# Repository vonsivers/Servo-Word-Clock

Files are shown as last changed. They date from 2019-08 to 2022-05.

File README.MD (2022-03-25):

# Servo Wordclock - Version 2

Wordclock controlled by 114 servos. Improved version 2

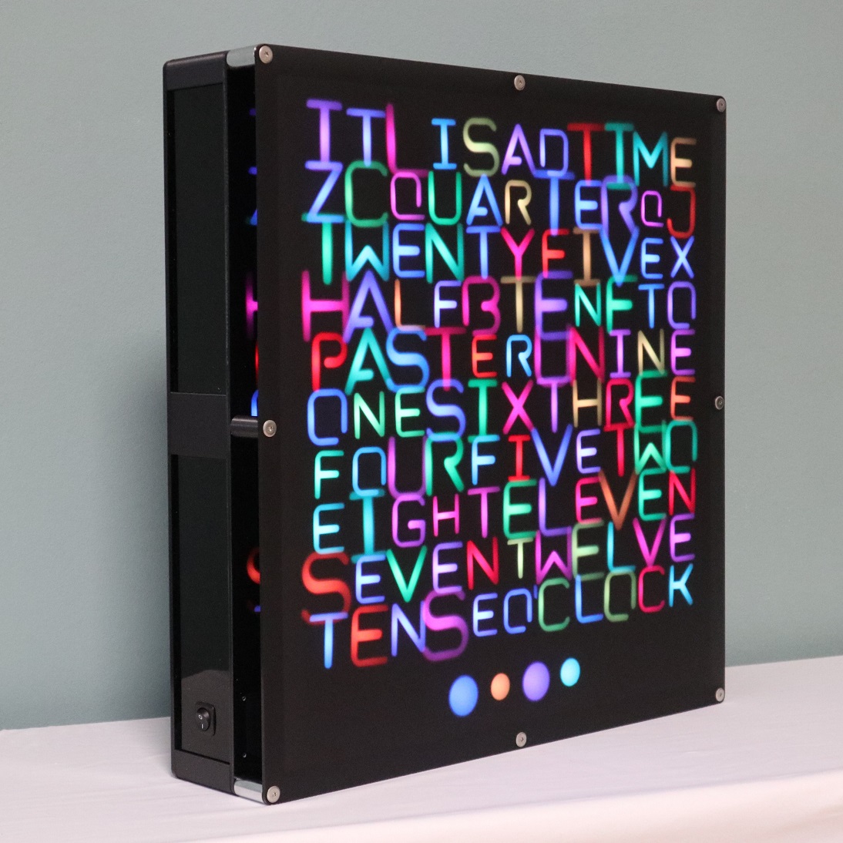
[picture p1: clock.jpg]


## BoM
see "BoM.xls"

## Detailed Build Instructions
see "Assembly Instructions.pdf"

## Laser Cut
see files in folder dxf

quantity, materials and thicknesses specified in BoM

## 3D Printing
see files in folder stl

quantity and recommended materials specified in BoM

stl files named "Any" have slightly looser tolerances

## PCBs
see folder PCBs

LED_board was ordered as PCBA from PCBWay.com with black solder mask

wordclock_mainPCB was ordered as bare PCB from aisler.net

## Links
[demo video on YouTube](https://youtu.be/Euf8V2k0oOI)

[Hackaday.io project link](https://hackaday.io/project/166546-servo-controlled-word-clock-v2)

[Instructables project link](https://www.instructables.com/Servo-Wordclock-V2/)

[Version 1 Instructables project link](https://www.instructables.com/Word-Clock-Controlled-by-114-Servos/)

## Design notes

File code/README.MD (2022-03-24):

# Servo Word Clock GUI - Version 2
> Code for Servo Word Clock for ESP8266

Allows control of clock via webserver that runs on ESP. GUI based on preact material UI. 

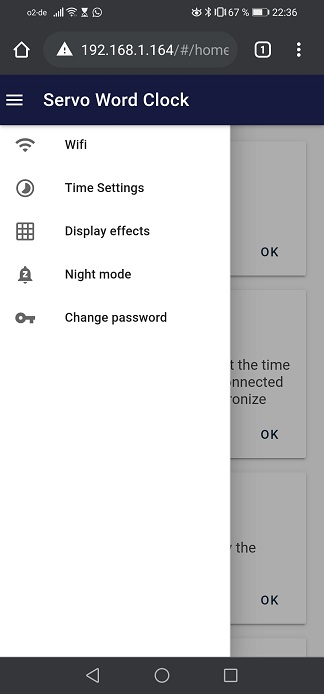
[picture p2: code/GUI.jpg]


## Build

- Install [node js](https://nodejs.org/en/)

- open terminal in folder "servowordclock-gui-develop"

```sh
npm i

npm run build
```

## Code Upload

- Install Arduino IDE

- Install ESP8266 addon

- Install ESP8266LittleFS tool

- Install required libraries
	- https://github.com/me-no-dev/ESPAsyncTCP
	- https://github.com/me-no-dev/ESPAsyncWebServer
	- https://github.com/adafruit/Adafruit-PWM-Servo-Driver-Library
	- https://github.com/FastLED/FastLED

- in Arduino IDE select Tools -> Boards -> ESP8266 Boards -> Node MCU 1.0 (ESP-12E)

- Upload LittleFS Data using Arduino IDE

- Upload code to ESP using Arduino IDE

- Once code has been uploaded following updates can be done via Wifi (OTA) with password "ServoWordClockOTA"

## Code Manual

see Manual.pdf

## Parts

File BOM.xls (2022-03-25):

# | Name | Description | Qty | Type | Material | comment | included in Kit | source | Item No.
1 | Screen V3_4 | 3mm thickness | 1 | Lasercut | Acrylic, grey, frosted, translucent |  | yes | https://expresszuschnitt.de/Acrylglas-satiniert-grau | AGS-9T23XX
2 | Frame V3_4 | 5mm thickness | 1 | Lasercut | Acrylic, black |  | yes | snijlab.nl
3 | Backplate V3_4 | 5mm thickness | 1 | Lasercut | Acrylic, black or clear |  | yes | snijlab.nl
4 | Cover | 3mm thickness | 7 | Lasercut | Acrylic, black or clear |  | yes | snijlab.nl
5 | Cover Switch | 3mm thickness | 1 | Lasercut | Acrylic, black or clear |  | yes | snijlab.nl
6 | Corner Column V3_4 |  | 3 | 3D-Print | PETG/PLA | PETG recommend | no | /
7 | Corner Column Cable V3_4 |  | 1 | 3D-Print | PETG/PLA | PETG recommend | no | /
8 | Top Down Column V3_4 |  | 2 | 3D-Print | PETG/PLA | PETG recommend | no | /
9 | Side Column V3_4 |  | 2 | 3D-Print | PETG/PLA | PETG recommend | no | /
10 | Corner Column Front V3_4 |  | 4 | 3D-Print | PETG/PLA | PETG recommend | no | /
11 | Cable Holder V3_5 |  | 1 | 3D-Print | PETG/PLA |  | no | /
12 | Screw Cover V3_5 |  | 2 | 3D-Print | PETG/PLA |  | no | /
13 | Housing 4x V3_5 |  | 1 | 3D-Print | PETG/PLA | PETG recommend | no | /
14 | Spur Gear M1 Z20 - V3_4 |  | 4 | 3D-Print | PETG/PLA | PETG recommend "may need be adjusted according to printer tolerances, fitting to Housing and Gear" | no | /
15 | Spur Rack V3_5 |  | 114 | 3D-Print | PETG/PLA | PETG recommend "may need be adjusted according to printer tolerances, fitting to Housing and Gear" | no | /
16 | Housing V3_5 Top |  | 11 | 3D-Print | PETG/PLA | PETG recommend | no | /
17 | Housing V3_5 Bottom |  | 11 | 3D-Print | PETG/PLA | PETG recommend | no | /
18 | Standoff M2,5 x 2,5 |  | 44 | 3D-Print | PETG/PLA |  | no | /
19 | Standoff M3 x 5 |  | 4 | 3D-Print | PETG/PLA |  | no | /
20 | Standoff M2,5 x 5,5 |  | 3 | 3D-Print | PETG/PLA |  | no | /
21 | A V3_2 |  | 4 | 3D-Print | PETG/PLA |  | no | /
22 | B V3_2 |  | 1 | 3D-Print | PETG/PLA |  | no | /
23 | C V3_2 |  | 3 | 3D-Print | PETG/PLA |  | no | /
24 | D V3_2 |  | 1 | 3D-Print | PETG/PLA |  | no | /
25 | E V3_2 |  | 21 | 3D-Print | PETG/PLA |  | no | /
26 | F V3_2 |  | 5 | 3D-Print | PETG/PLA |  | no | /
27 | G V3_2 |  | 1 | 3D-Print | PETG/PLA |  | no | /
28 | H V3_2 |  | 3 | 3D-Print | PETG/PLA |  | no | /
29 | I V3_2 |  | 8 | 3D-Print | PETG/PLA |  | no | /
30 | J V3_2 |  | 1 | 3D-Print | PETG/PLA |  | no | /
31 | K V3_2 |  | 1 | 3D-Print | PETG/PLA |  | no | /
32 | L V3_2 |  | 5 | 3D-Print | PETG/PLA |  | no | /
33 | M V3_2 |  | 1 | 3D-Print | PETG/PLA |  | no | /
34 | N V3_2 |  | 8 | 3D-Print | PETG/PLA |  | no | /
35 | O V3_2 |  | 5 | 3D-Print | PETG/PLA |  | no | /
36 | O' V3_2 |  | 1 | 3D-Print | PETG/PLA |  | no | /
37 | P V3_2 |  | 1 | 3D-Print | PETG/PLA |  | no | /
38 | Point V3_2 |  | 4 | 3D-Print | PETG/PLA |  | no | /
39 | Q V3_2 |  | 2 | 3D-Print | PETG/PLA |  | no | /
40 | R V3_2 |  | 5 | 3D-Print | PETG/PLA |  | no | /
41 | S V3_2 |  | 5 | 3D-Print | PETG/PLA |  | no | /
42 | T V3_2 |  | 13 | 3D-Print | PETG/PLA |  | no | /
43 | U V3_2 |  | 3 | 3D-Print | PETG/PLA |  | no | /
44 | V V3_2 |  | 5 | 3D-Print | PETG/PLA |  | no | /
45 | W V3_2 |  | 3 | 3D-Print | PETG/PLA |  | no | /
46 | X V3_2 |  | 2 | 3D-Print | PETG/PLA |  | no | /
47 | Y V3_2 |  | 1 | 3D-Print | PETG/PLA |  | no | /
48 | Z V3_2 |  | 1 | 3D-Print | PETG/PLA |  | no | /
49 | Diffusor Film - Aslan D160 | Folie Aslan D160 49x48 cm | 1 | Foil | PVC |  | yes | https://www.ifoha.de/shop/spezialfolien/folien-fuer-werbetechnik/leuchtkastenfolie/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 | 14160
50 | Wordclock LED PCB | PCBA | 114 | PCBA | div. | Servo-Word-Clock\PCBs\LED_board | yes | PCBway.com
51 | Wordclock Main PCB | bare PCB | 1 | PCB | div. | Servo-Word-Clock\PCBs\wordclock_mainPCB | yes | aisler.net
52 | ESP8266 Dev Board | NodeMCU Lua Amica Modul V2 ESP8266 ESP-12F WIFI | 1 | PCBA | div. |  | yes | https://www.az-delivery.de/products/nodemcu?variant=27600517385
53 | TXS0108E v1 | 8 ch logic level converter | 1 | PCBA | div. |  | yes | https://www.az-delivery.de/products/logiklevel-wandler-3-3v-5v?variant=18568538390624
54 | Resistor, 470 Ohm | Through Hole | 1 | Electronics | div. |  | yes | https://www.conrad.de/de/p/tru-components-tc-cfr0w4j0471a50203-kohleschicht-widerstand-470-axial-bedrahtet-0207-0-25-w-5-1-st-1584807.html
55 | Electrolytic Capacitor, 6.3V, 1000µF | Through Hole | 1 | Electronics | div. |  | yes | https://www.conrad.de/de/p/teapo-ksh108m016s1a5g20k-elektrolyt-kondensator-radial-bedrahtet-3-5-mm-1-000-f-16-v-20-x-h-8-mm-x-20-mm-1-st-1590551.html
56 | JST XH2.54 connector, male, 2-pin | Through Hole | 1 | Electronics | div. |  | yes | https://www.ebay.de/itm/173782755881?hash=item2876426a29:g:E0QAAOSwliBgG6Ys
57 | JST XH2.54 connector, male, 3-pin | Through Hole | 1 | Electronics | div. |  | yes | https://www.ebay.de/itm/173782755881?hash=item2876426a29:g:E0QAAOSwliBgG6Ys
58 | male pin header, 2.54mm, 3-pin |  | 1 | Electronics | div. |  | yes | https://www.ebay.de/itm/255283310862
59 | Current Distributor V2x12 |  | 2 | PCBA | div. |  | yes | https://www.pollin.de/ | 452459
60 | PCA9685 PWM driver | 12 Channel PWM driver | 11 | PCBA | div. |  | yes | https://www.az-delivery.de/products/pca9685-servotreiber?variant=6126640889883
61 | Male Pin Header 6-Pin | angled/horizontal | 11 | Electronics | div. |  | yes | https://www.mouser.de/ | 649-68016-406HLF
62 | Servo - SG90 |  | 114 | Servodrive | div. | 6 spare pcs included in kit | yes | https://de.aliexpress.com
63 | Rocker Switch - Conrad - 1587816 | TRU COMPONENTS Wippschalter TC-R13-135A-02 250 V/AC 10 A 1 x Aus/Ein rastend 1 St. | 1 | Electronics | div. |  | yes | https://www.conrad.de/de/p/tru-components-wippschalter-tc-r13-135a-02-250-v-ac-10-a-1-x-aus-ein-rastend-1-st-1587816.html
64 | Zip Tie Mount |  | 93 | OTS | PA6 |  | yes | https://www.ebay.de/
65 | Rampa - KF M6x16 |  | 12 | Screw | Steel, black |  | yes | https://www.rampa.com/de/de/
66 | Rampa - KF M6x90 |  | 4 | Screw | Steel, black |  | yes | https://www.rampa.com/de/de/
67 | ISO 7380 - M3 x 12 |  | 4 | Screw | Steel, black |  | yes | schraube-mutter.de
68 | ISO 7380 - M4 x 8 |  | 1 | Screw | Steel, black |  | yes | schraube-mutter.de
69 | ISO 10642 - M4 x 12 |  | 24 | Screw | Steel, black |  | yes | schraube-mutter.de
70 | ISO 7045 - M2,5 x 4 | included with servo | 114 | Screw | Steel |  | yes | /
71 | ISO 7049 - ST2,2 x 6 |  | 376 | Screw | Steel |  | yes | https://www.schraubenhimmel.de/detail/index/sArticle/47778
72 | ISO 7049 - ST2,2 x 6,5 | included with servo | 228 | Screw | Steel |  | yes | /
73 | ISO 4762 - M2,5 x 12 |  | 3 | Screw | Steel, black |  | yes | schraube-mutter.de
74 | Zip Ties |  | 100 | OTS | PA6 |  | yes | https://www.ebay.de/
75 | Cable sleeve 0.34mm² |  | 18 | Electronics | div. |  | yes | https://www.conrad.de/de/p/tru-components-1091301-aderendhuelse-1-x-0-34-mm-x-6-mm-teilisoliert-tuerkis-100-st-1567720.html | 1567720 - VQ
76 | Cable sleeve 0.22mm² |  | 22 | Electronics | div. |  | yes | https://www.conrad.de/de/p/tru-components-1091302-aderendhuelse-1-x-0-25-mm-x-6-mm-teilisoliert-violett-100-st-1571001.html | 1571001 - VQ
77 | power supply, 5V, 5A | Mean Well GST40A05-P1J power supply, 5 V/DC, 5 A, 25 W | 1 | Electronics | div. |  | yes | https://www.conrad.de/de/p/mean-well-gst40a05-p1j-tischnetzteil-festspannung-5-v-dc-5-a-25-w-1439222.html | 1439222 - VQ
78 | Mainpower Cable 230/110V |  | 1 | Cable | div. | depends on region | yes | https://www.conrad.de
79 | Cable Mainpower 5V with plug | DC cable, 5.50 mm, 2.10 mm, plug - open end, 1 m | 1 | Cable | div. |  | yes | https://www.conrad.de/de/p/tru-components-niedervolt-anschlusskabel-niedervolt-buchse-kabel-offenes-ende-5-50-mm-2-10-mm-1-m-1-st-1715115.html | 1715115 - VQ
80 | Cable 5V-Block | Cable, red, 0.34mm², open end - sleeve, 7.5 cm | 1 | Cable | div. | DIY | yes | /
81 | Cable 5V Block-Block | Cable, red, 0.34mm², sleeve - sleeve, 12 cm | 1 | Cable | div. | DIY | yes | /
82 | Cable Gnd Block-Block | Cable, black, 0.34mm², sleeve - sleeve, 12 cm | 1 | Cable | div. | DIY | yes | /
83 | Cabel LED-LED short | Cable JST XH2.54, 3-pole, female-female, 7.5 cm, 22AWG | 103 | Cable | div. |  | yes | https://de.aliexpress.com/store/5031112?spm=a2g0s.9042311.0.0.77f84c4dC5KDAi
84 | Cable LED-LED long | Cable JST XH2.54, 3-pole, female-female, 55 cm, 22AWG | 12 | Cable | div. |  | yes | https://de.aliexpress.com/store/5031112?spm=a2g0s.9042311.0.0.77f84c4dC5KDAi
85 | Cable 1st Sboard | Cable Dupont, 3-pole, female-female, 25 cm | 1 | Cable | div. |  | yes | https://de.aliexpress.com/item/33030664287.html?spm=a2g0s.9042311.0.0.70284c4ds6bReA
86 | Cable Sboard-Sboard | Cable Dupont, 6-pole, female-female, 10 cm | 10 | Cable | div. |  | yes | https://de.aliexpress.com/item/33030664287.html?spm=a2g0s.9042311.0.0.70284c4ds6bReA
87 | Cable Sboard-5V | Cable, red, 0.22mm², sleeve - sleeve, ca. 25 cm | 11 | Cable | div. | DIY, varying length | yes | /
88 | Cable Sboard-Gnd | Cable, black, 0.22mm², sleeve - sleeve, ca. 25 cm | 11 | Cable | div. | DIY, varying length | yes | /
89 | Cable Main PCB Power | Cable JST XH2.54, 2-pole, female-sleeve, 10 cm, 22AWG | 1 | Cable | div. |  | yes | /
90 | Glueing Tool |  | 1 | 3D-Print | PETG/PLA |  | no | /
91 | Alignment Jig |  | 1 | 3D-Print | PETG/PLA |  | no | /

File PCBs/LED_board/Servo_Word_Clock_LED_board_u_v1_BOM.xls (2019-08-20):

 |  |  | Servo Word Clock LED board u v1 BOM
Item # | *Ref Des | *Qty | Manufacturer | *Mfg Part # | Description / Value | *Package | Type | Your Instructions / Notes
1 | U1 | 1 | Worldsemi Co Limited | WS2812B | LED, SMD, 5050,PLCC4, RGB | PLCC4 | SMD
2 | C1 | 1 | Murata | GCJ188R71C104KA01D | CAP CER 0.1UF 16V 10% X7R 0603 | 0603 | SMD
3 | J1,J2 | 2 | JST | B3B-XH-A(LF)(SN) | CONN HEADER VERT 3POS 2.5MM | 3POS | thru-hole | Assembled on bottom side!
Need a quick and accurante quote? Need an efficient production? Please read?MT Ordering Necessary Files & Info?n 1 minute. Thank you very much!
Click for Instructions on How to Create a BOM

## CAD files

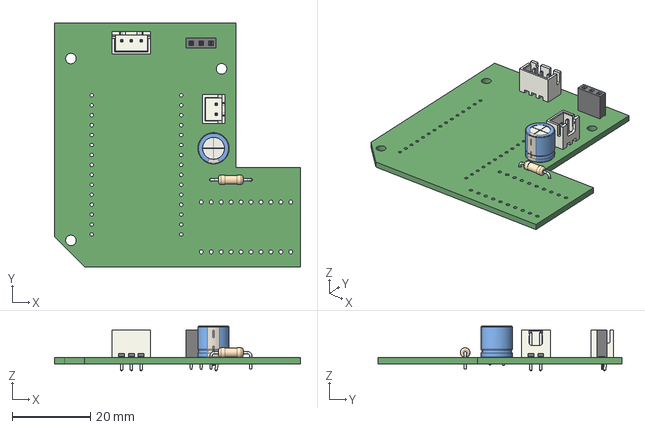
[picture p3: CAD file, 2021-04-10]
PCBs/wordclock_mainPCB/wordclock_mainPCB.step
62.9 x 62.2 x 11.4 mm

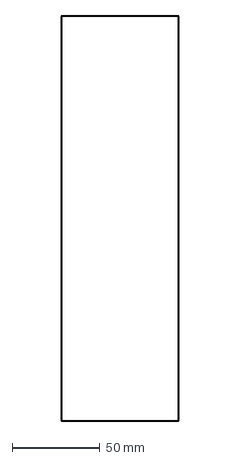
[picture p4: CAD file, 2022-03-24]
dxf/Cover.dxf
67.0 x 231.0 mm

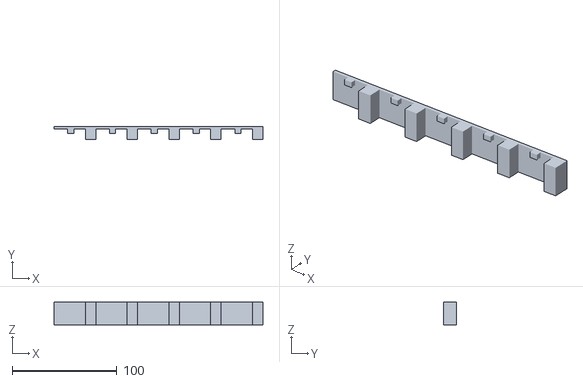
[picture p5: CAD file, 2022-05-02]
stl/alignment jig.stl
200.0 x 12.5 x 22.0

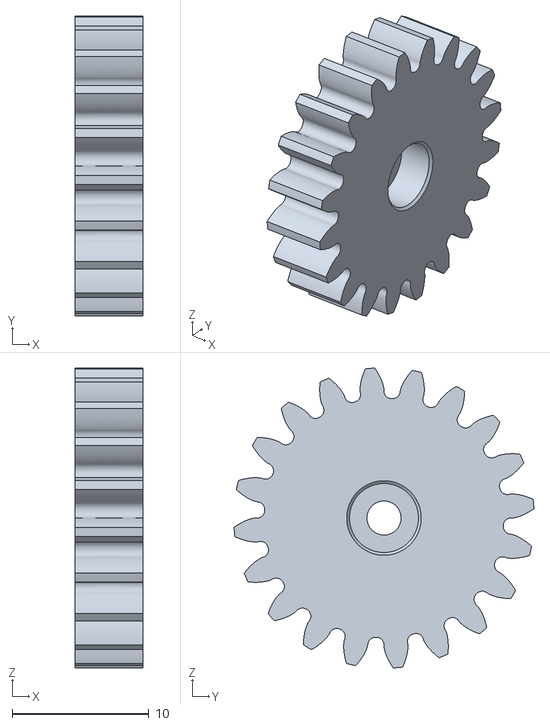
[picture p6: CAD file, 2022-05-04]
stl/Letter/Spur Gear M1 Z20 - D5,05.stl
5.00 x 22.0 x 22.0

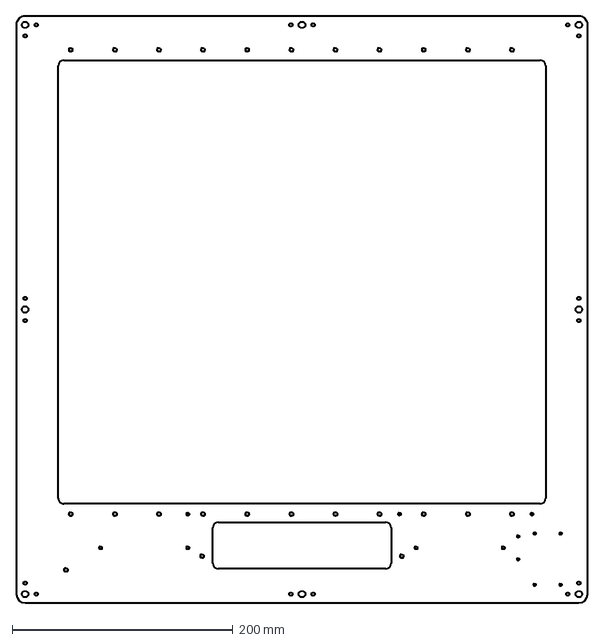
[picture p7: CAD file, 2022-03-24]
dxf/Frame V3_4.dxf
518.0 x 532.0 mm

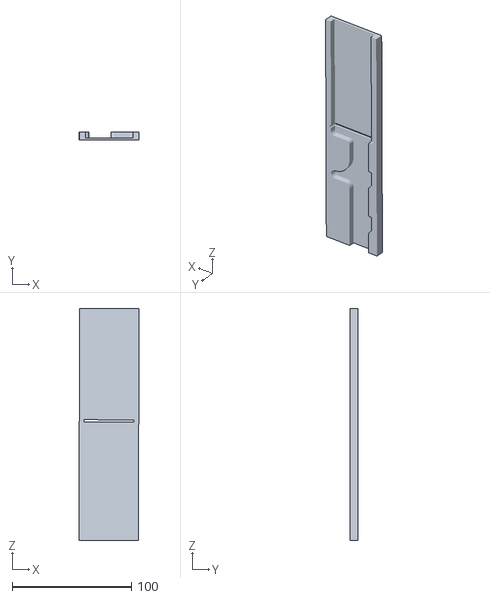
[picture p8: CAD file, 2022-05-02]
stl/glueing jig.stl
50.5 x 7.06 x 194.3

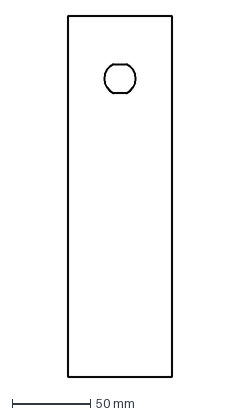
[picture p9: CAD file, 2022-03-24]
dxf/Cover Switch.dxf
67.0 x 231.0 mm

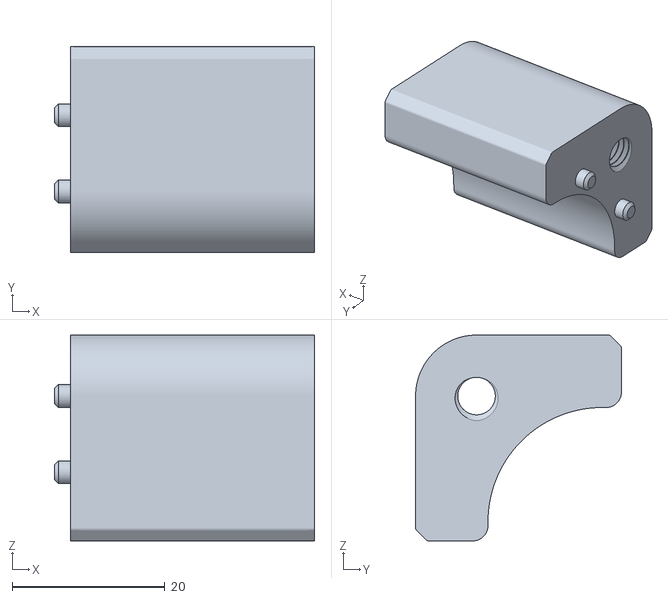
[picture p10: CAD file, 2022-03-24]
stl/Corner Column Front V3_4.stl
34.1 x 27.0 x 27.0

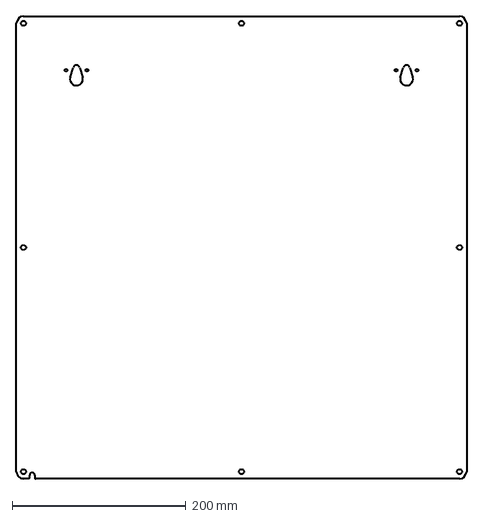
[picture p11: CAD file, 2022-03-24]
dxf/Backplate V3_4.dxf
518.0 x 532.0 mm

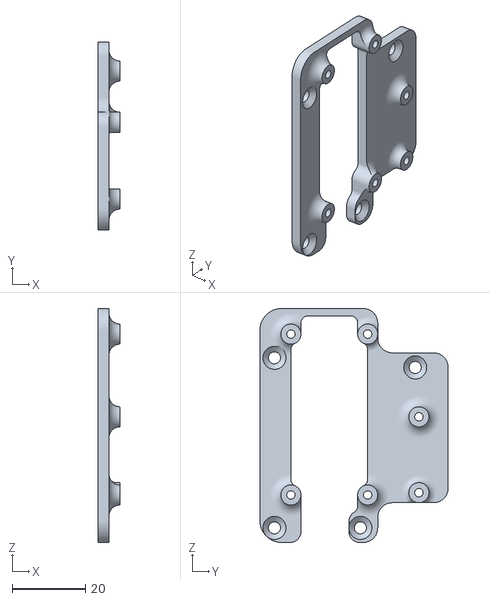
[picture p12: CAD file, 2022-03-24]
stl/ESP Holder V2.stl
6.00 x 51.5 x 64.0

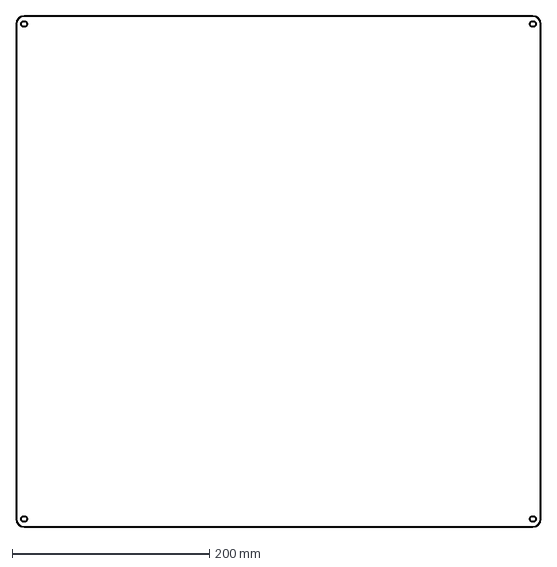
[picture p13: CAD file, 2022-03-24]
dxf/Screen V3_4.dxf
532.0 x 518.0 mm

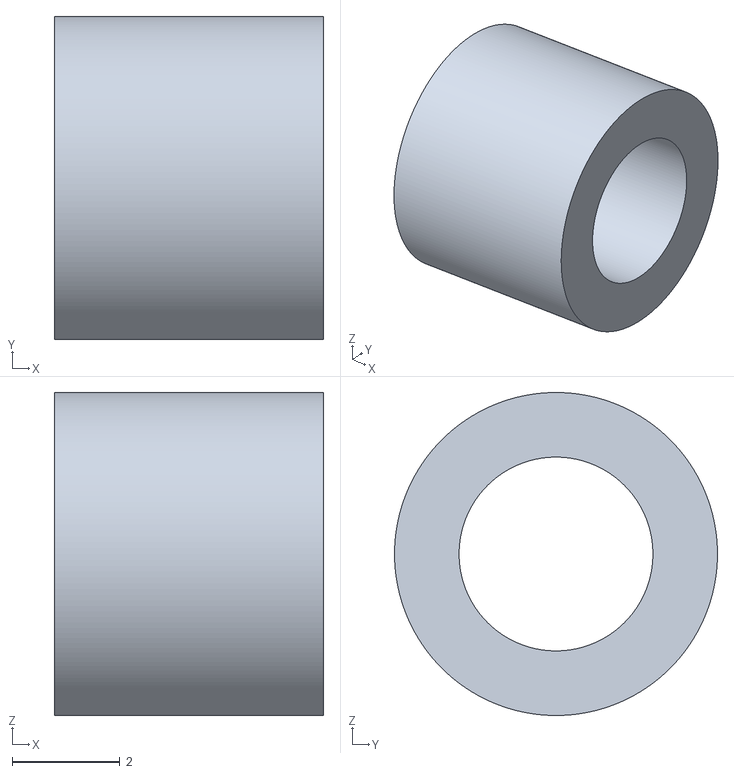
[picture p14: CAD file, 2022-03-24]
stl/Standoff M3 x 5.stl
5.00 x 6.00 x 6.00

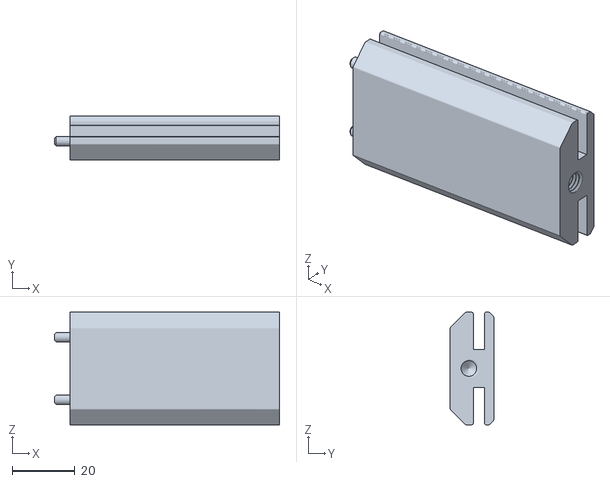
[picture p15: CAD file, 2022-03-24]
stl/Top Down Column V3_4 Any.stl
71.9 x 14.0 x 36.0

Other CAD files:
stl/Letter/Spur Gear M1 Z20 - D5,1.stl
stl/Letter/Spur Gear M1 Z20 - D5.stl
stl/Letter/Spur Gear M1 Z20 - D4,85.stl
stl/Letter/Spur Gear M1 Z20 - D4,95.stl
stl/Letter/Spur Gear M1 Z20 - D4,9.stl
stl/Cable Holder V3_5.stl
stl/Corner Column Cable V3_4 Any.stl
stl/Corner Column Cable V3_4.stl
stl/Corner Column V3_4 Any.stl
stl/Corner Column V3_4.stl
stl/Letter/A V3_15.stl
stl/Letter/B V3_15.stl
stl/Letter/C V3_15.stl
stl/Letter/D V3_15.stl
stl/Letter/E V3_15.stl
stl/Letter/F V3_15.stl
stl/Letter/G V3_15.stl
stl/Letter/H V3_15.stl
stl/Letter/I V3_15.stl
stl/Letter/J V3_15.stl
stl/Letter/K V3_15.stl
stl/Letter/L V3_15.stl
stl/Letter/M V3_15.stl
stl/Letter/N V3_15.stl
stl/Letter/O V3_15.stl
stl/Letter/O' V3_15.stl
stl/Letter/P V3_15.stl
stl/Letter/Point V3_15.stl
stl/Letter/Q V3_15.stl
stl/Letter/R V3_15.stl
stl/Letter/S V3_15.stl
stl/Letter/T V3_15.stl
stl/Letter/U V3_15.stl
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

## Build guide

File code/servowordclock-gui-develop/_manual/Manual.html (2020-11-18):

 User Manual



User Manual

Introduction

Setting up the Clock

Access User Interface

Timezone Configuration

Manual Time Setting

Display Settings

Night Mode Settings

## Introduction

The Servo Wordclock was designed to be connected to your local WiFi and can be controlled via a web based user interface. With internet access the clock will also automatically keep time by synchronizing to an NTP server.

If there is no WiFi network available the clock will create a WiFi access point to which other devices can connect.

The user interface can be used to control all clock functions like WiFi configuration, time setting, display brightness, color and animations.

All settings will be permanently stored on the clock’s non-volatile memory.

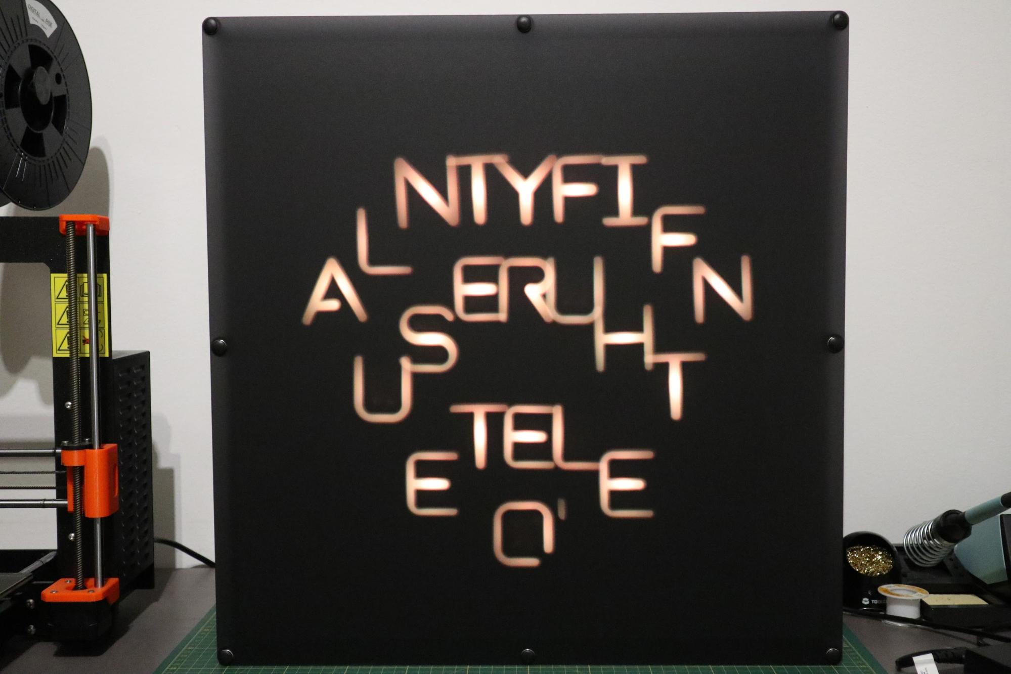
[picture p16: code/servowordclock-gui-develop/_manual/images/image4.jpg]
## Setting up the Clock 

- Connect the clock to the included power supply
- To turn on the clock use the switch located on the lower left side. The clock will need about 30 seconds to initialize all servo motors
- When the clock was switched on for the first time it will create a WiFi access point. When the access point is active the clock will show a yellow WiFi symbol on the screen

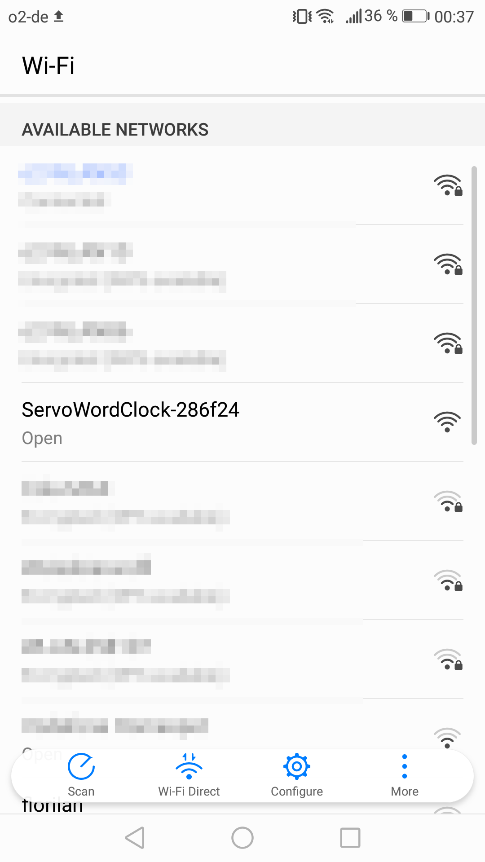
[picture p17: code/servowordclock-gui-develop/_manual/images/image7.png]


- Search for new networks on your PC or mobile device, you should see a network named ServoWordClock-xxxxxx to which you can connect without password
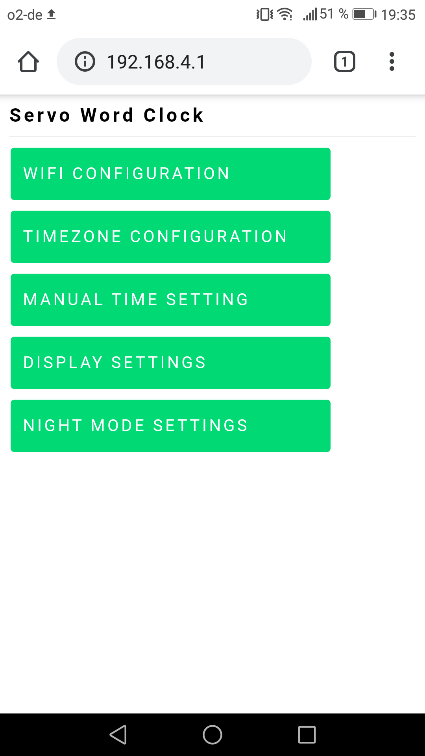
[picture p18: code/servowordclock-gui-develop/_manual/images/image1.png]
- Once you are connected to the clock’s access point open a web browser. In the address bar type in the IP address 192.168.4.1. this will open the clock’s user interface 
- Click on the WIFI CONFIGURATION button this will bring you to the WIFI settings page

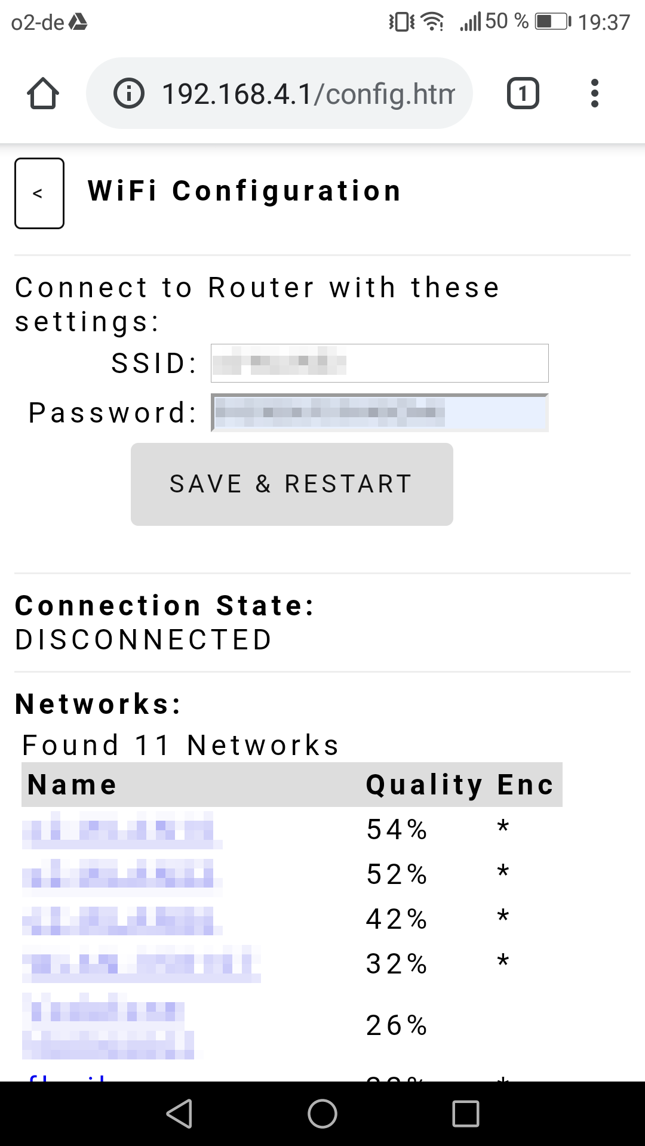
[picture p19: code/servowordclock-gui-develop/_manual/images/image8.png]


- After the network search has finished select your local WiFi network from the list and enter the password. After that click SAVE & RESTART to save the settings to the clock’s memory and reboot
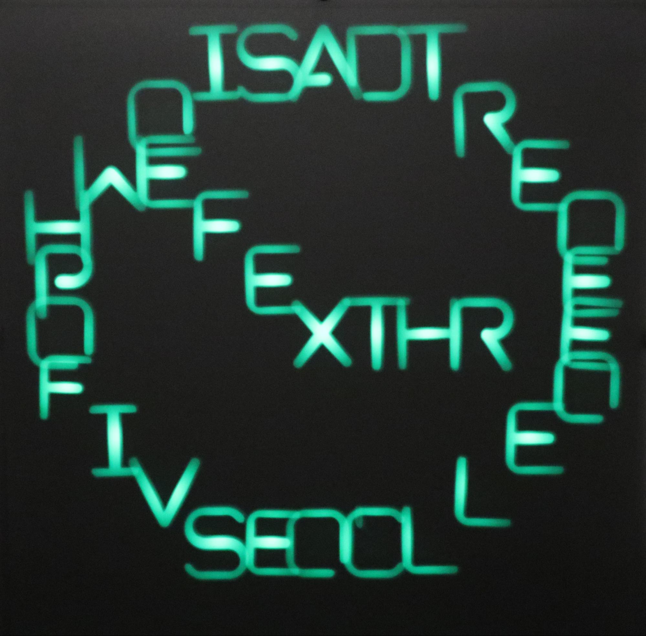
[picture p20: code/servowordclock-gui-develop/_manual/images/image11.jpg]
- After the clock has restarted it will try to connect to your local WiFi. When the connection was successful a green clock symbol will be shown on the screen until the time has been synchronized with the NTP server 
- If the clock cannot connect to your WiFi network it will revert to opening an access point

## Access User Interface

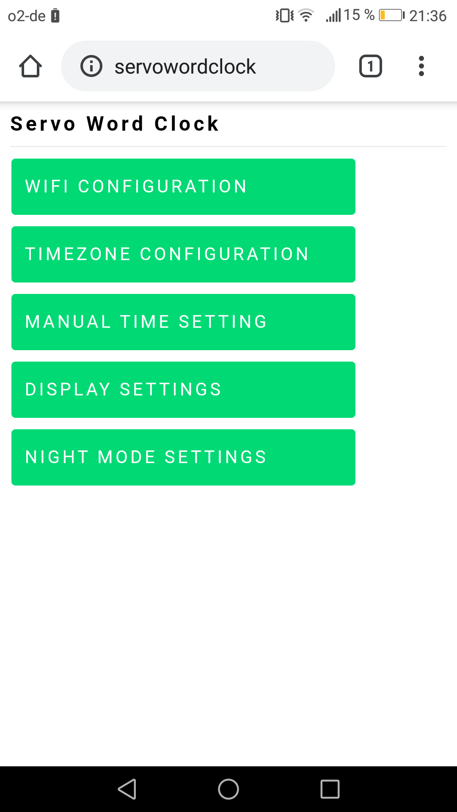
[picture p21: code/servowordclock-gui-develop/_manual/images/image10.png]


- If the clock is connected to your local WiFi you can access the user interface from any PC or mobile device within that network via your web browser.

On Windows, OSX, Linux and iOS type servowordclock.local in your address bar.

On Android systems just type servowordclock instead[1]

- If the clock has no WiFi connection you can access the user interface by connecting to the clock’s own access point (see Chapter 2)
- If the clock loses its WiFi connection during operation it will automatically try to reconnect. When the connection still fails the clock will restart and open an access point

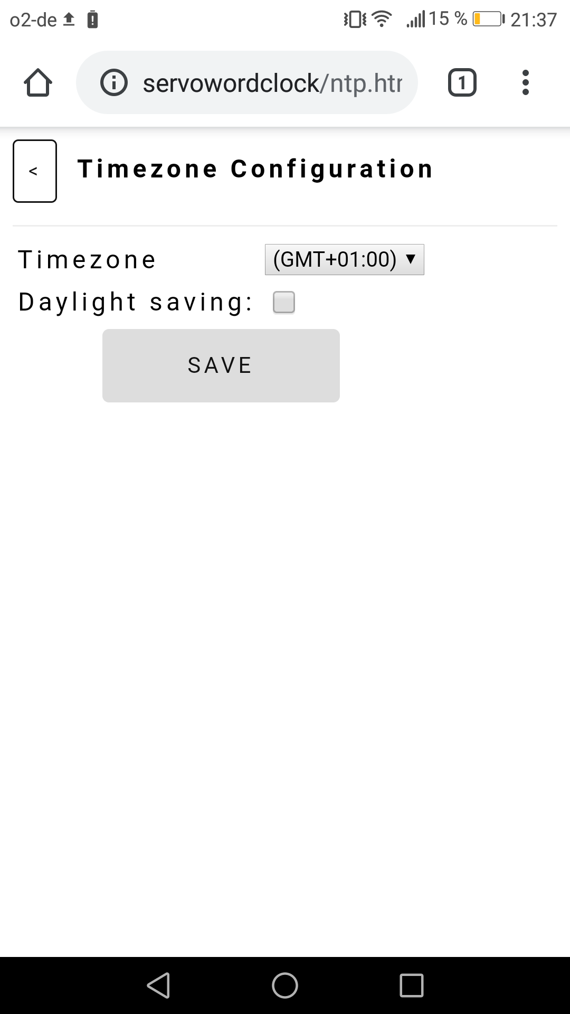
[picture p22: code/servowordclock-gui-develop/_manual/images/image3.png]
### Timezone Configuration 

- Use the TIMEZONE CONFIGURATION page to enter your local timezone. If your country observes daylight saving time also check the daylight saving box. Clicking SAVE will update the timezone and store it to the clock’s memory

### Manual Time Setting

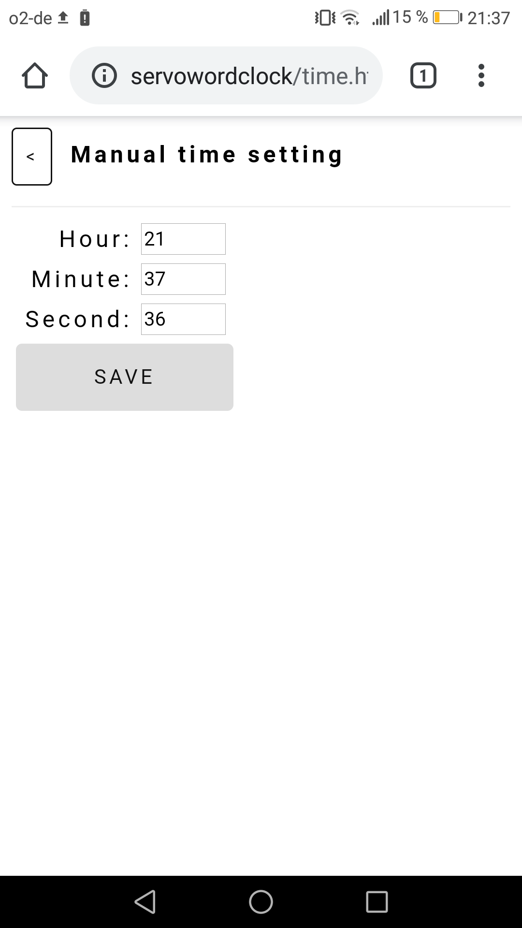
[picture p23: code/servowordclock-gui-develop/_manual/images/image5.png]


- If your clock is not connected to the internet or cannot synchronize to the NTP server you can use this page to set the time manually[2]. The time will only be updated after clicking SAVE

### Display Settings

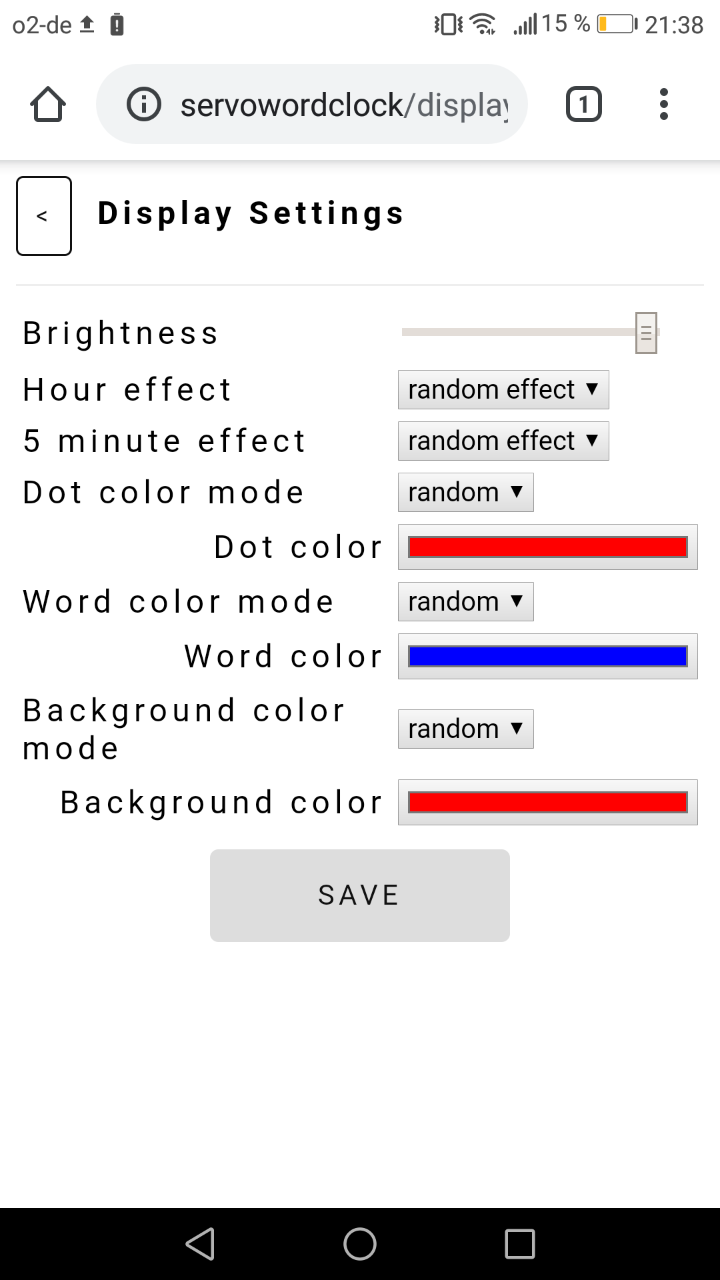
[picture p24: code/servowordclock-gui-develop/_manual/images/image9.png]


- The DISPLAY SETTINGS page can be used to change several options on how the clock displays time
- Brightness: adjusts the brightness of all LEDs
- Hour effect: selects the animation that is used to display the time every full hour. Four different effects can be used typing, fade-in, fade-out, colormix. When set to random effect one of the four effects will be randomly selected
- 5 minute effect: selects the display animation that is shown every 5 minutes. Options are similar to Hour effect
- Dot color mode: when fixed is selected the color of the minute dots can be specified in the next row. Selecting random will use a random color each time the clock updates time
- Dot color: color of the minute dots when fixed is selected above
- Word color mode: changes how the color of all words that are used to display the time is selected. Options are similar to Dot color mode
- Word color: color of words that display the time when fixed is selected above
- Background color mode: changes how the color of all background letters that are not used to display the time is selected. Options are fixed, random and cycle. The latter will slowly cycle the color of all background letters
- Background color: color of all background letters when fixed is selected above

Clicking SAVE will update the display and store all settings to the clock’s memory

### Night Mode Settings

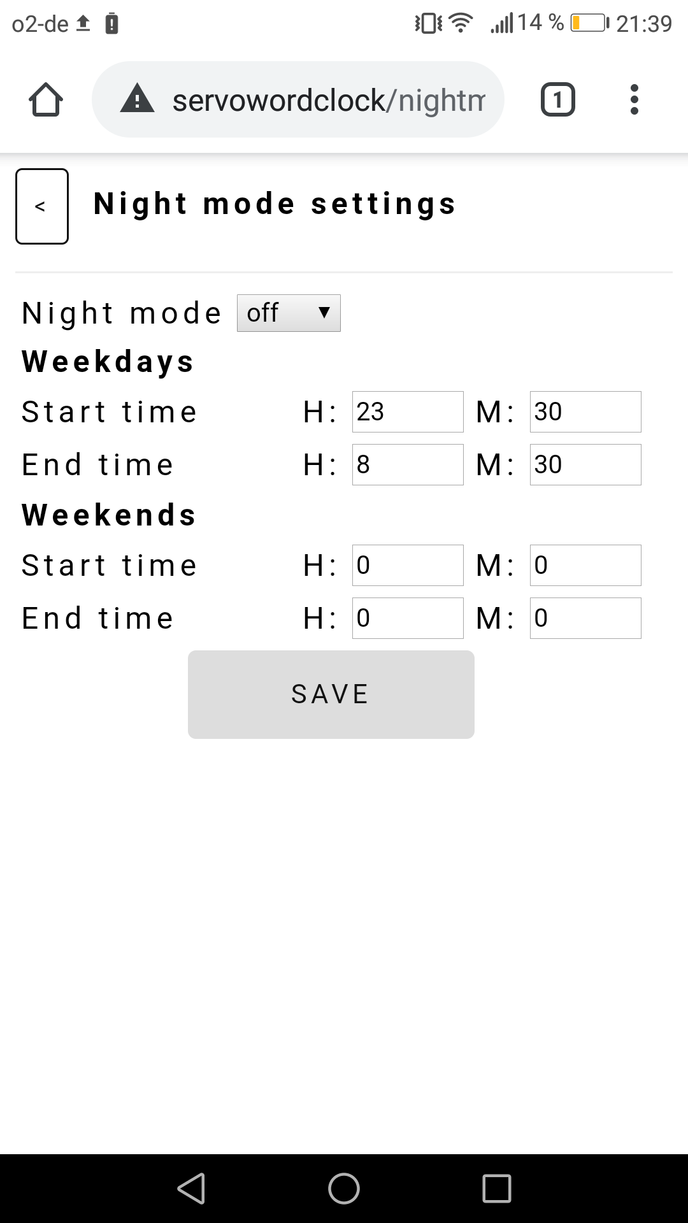
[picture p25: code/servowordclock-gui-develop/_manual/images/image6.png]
- The NIGHT MODE SETTINGS can be used to either switch of the servos or the entire clock for certain periods, e.g. during night or work hours. This will increase lifetime of the servos and may also be used to avoid being disturbed by the noise of the servos at nighttime 
- Night mode: selecting silent only switches off the servos, LEDs will still light up. The option off turns off the entire clock
- Start/End time: can be used to specify the start and end time when night mode is active. Separate periods for weekdays and weekends can be selected

Clicking SAVE will update the settings and store them to the clock’s memory

page v1 22-Nov-2019

[1] The user interface can also be reached by using the clock’s IP address. The clock does not use a fixed IP but one automatically assigned by your router. Please see the documentation of your router on how to find out the IP address of connected devices or follow this tutorial (https://www.howtogeek.com/204057/how-to-see-who%E2%80%99s-connected-to-your-wi-fi-network/).

[2] When the time is not regularly updated via NTP timekeeping may not be accurate

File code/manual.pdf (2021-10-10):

# User Manual

## Introduction Setting up the Clock User Interface

### Login Screen Change Password Time Settings

Automatic Time Setting
Manual Time Setting

### Display Settings Night Mode Settings

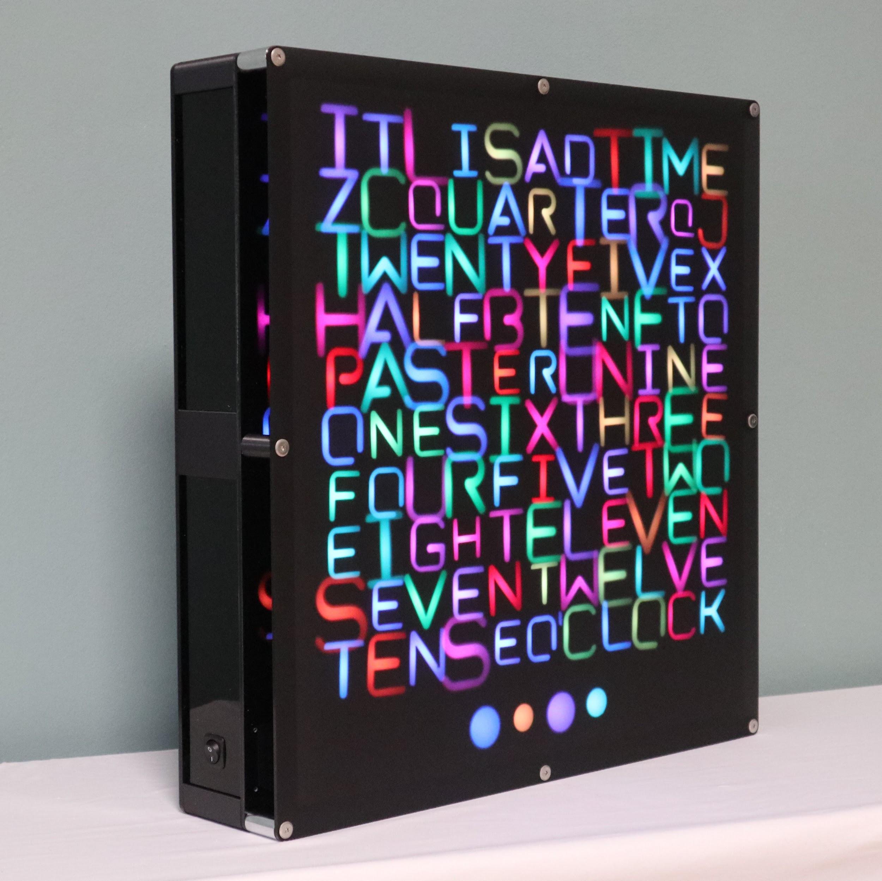
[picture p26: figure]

User Manual

## 1. Introduction

The Servo Wordclock was designed to be connected to your local WiFi and can be controlled via a web-based user interface. With internet access, the clock will also automatically keep time by synchronizing to an NTP server.
If there is no WiFi network available the clock will create a WiFi access point to which other devices can connect.
The user interface can be used to control all clock functions like WiFi configuration, time setting, display brightness, color, and animations.
All settings will be permanently stored in the clock’s non-volatile memory.

## 2. Setting up the Clock

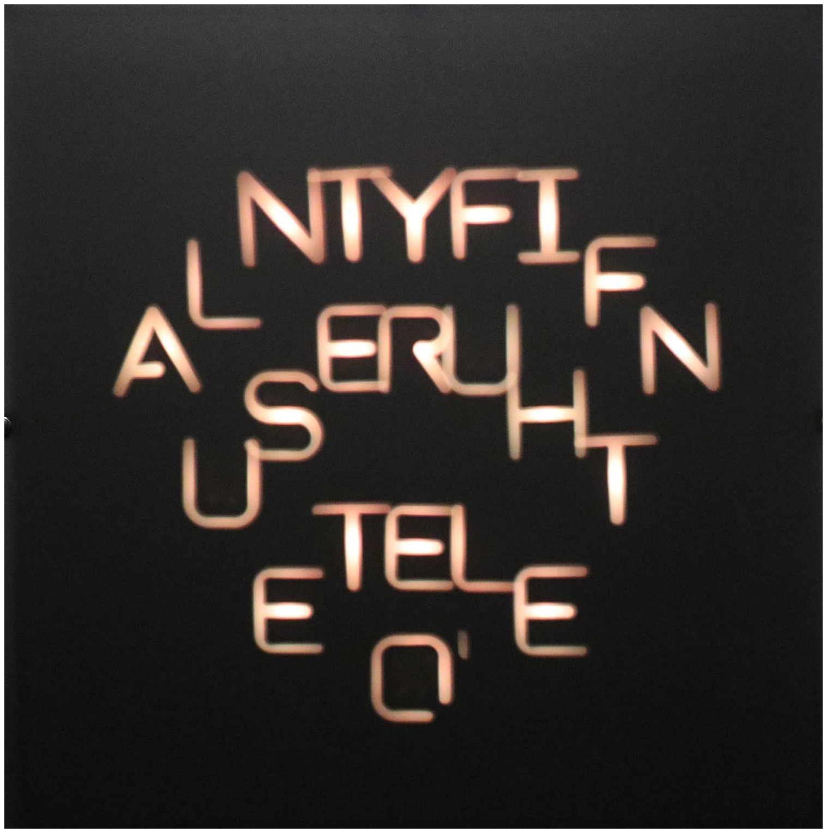
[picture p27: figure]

- Connect the clock to the included power supply
- To turn on the clock use the switch located on the lower left side. The clock will need about 30 seconds to initialize all servo motors
- When the clock was switched on for the first time it will create a WiFi access point. When the access point is active the clock will show a yellow WiFi symbol on the screen
- Search for new networks on your PC or mobile device, you should see a network named ServoWordClock-xxxxxx to which you can connect without a password

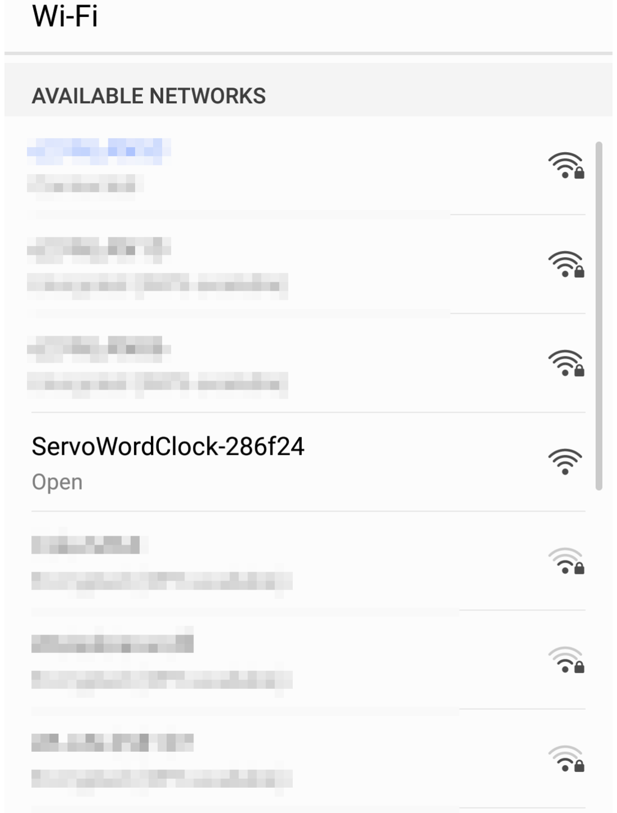
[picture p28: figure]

page 1 | v2 10-Oct-2021

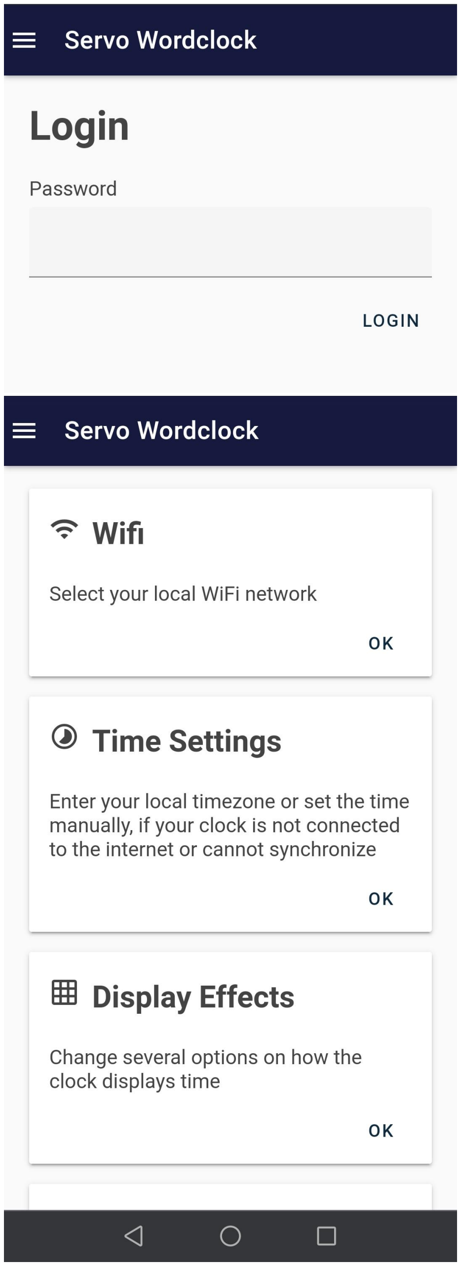
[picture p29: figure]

- Once you are connected to the clock’s access point open a web browser. In the address bar type in the IP address 192.168.4.1. this will open the clock’s login screen
- The default password to access the clock is 114servos. Type in this password and click LOGIN.
- You can now access all clock functions. If available, you should first connect the clock to your local WiFi network.
- Click on the WIFI button this will bring you to the WIFI settings page
page 2 | v2 10-Oct-2021

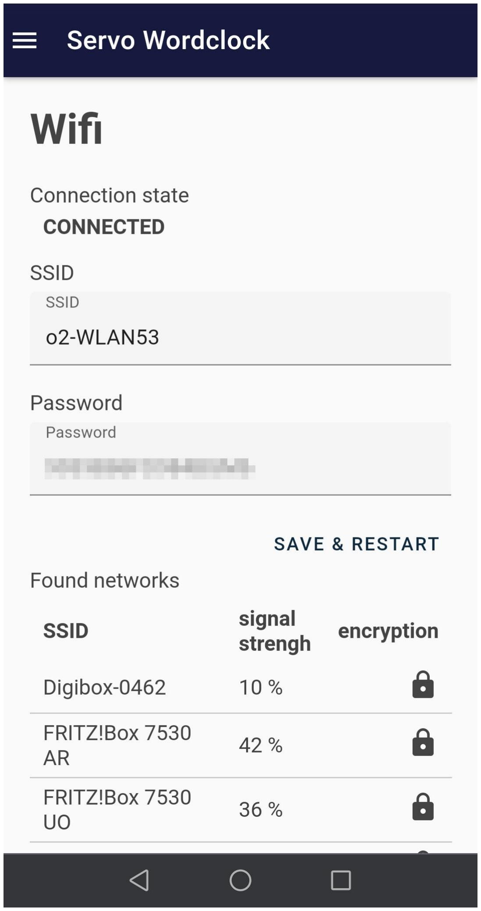
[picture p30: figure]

- After the network search has finished select your local WiFi network from the list and enter the password. After that click SAVE & RESTART to save the settings to the clock’s memory and reboot
page 3 | v2 10-Oct-2021

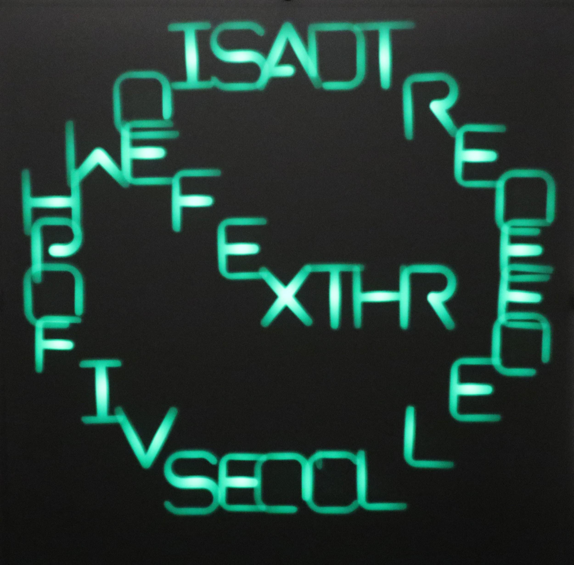
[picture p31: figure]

- After the clock has restarted it will try to connect to your local WiFi. When the connection was successful a green clock symbol will be shown on the screen until the time has been synchronized with the NTP server
- If the clock cannot connect to your WiFi network it will revert to opening an access point
page 4 | v2 10-Oct-2021

## 3. User Interface

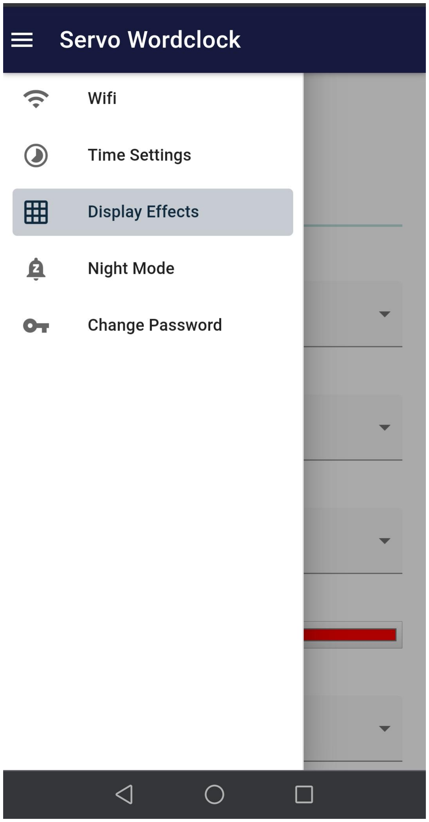
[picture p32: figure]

- If the clock is connected to your local WiFi you can access the user interface from any PC or mobile device within that network via your web browser.
On Windows, OSX, Linux and iOS type servowordclock.local in your address bar.
On Android systems you need to enter the clock’s IP address instead

1

- A convenient method to access the clock’s unser interface on mobile devices is to add it to your home screen. Once you have opened the clock’s user interface in your browser, e.g., Chrome tap the menu icon (3 dots symbol) and then tap “Add to home screen”
- If the clock has no WiFi connection you can access the user interface by connecting to the clock’s own access point and entering the IP address 192.168.4.1 (see Chapter 2)
- If the clock loses its WiFi connection during operation it will automatically try to reconnect. When the connection still fails the clock will restart and open an access point

1 The clock does not use a fixed IP but one automatically assigned by your router. Please see the documentation of your router on how to find out the IP address of connected devices or follow this tutorial. (https://www.howtogeek.com/204057/how-to-see-who%E2%80%99s-connected-to-your-wi-fi-network/)

page 5 | v2 10-Oct-2021

### 3.1. Login Screen

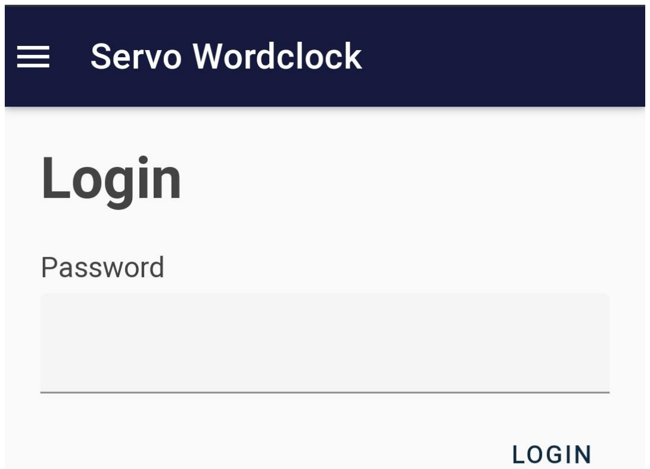
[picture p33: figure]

- When accessing the clock from your web browser you will always be prompted to enter a password. The default password is 114servos.

### 3.2. Change Password

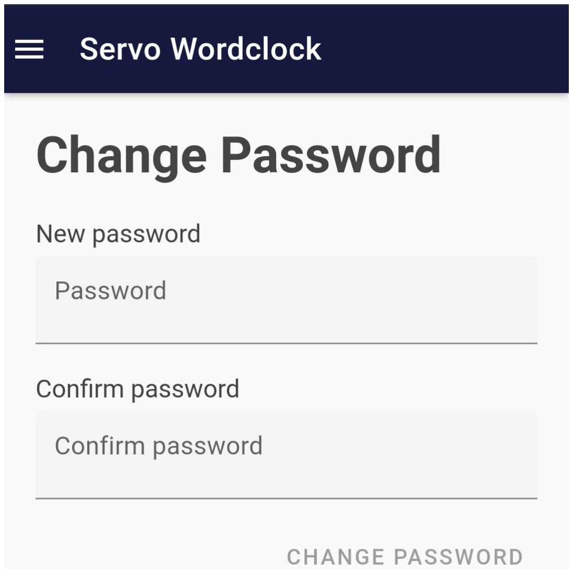
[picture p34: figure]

- To change the password enter the Change Password tab. Type in the new password and confirm it by typing it again in the field below then tap CHANGE
PASSWORD
page 6 | v2 10-Oct-2021

### 3.3. Time Settings

3.3.1. Automatic Time Setting

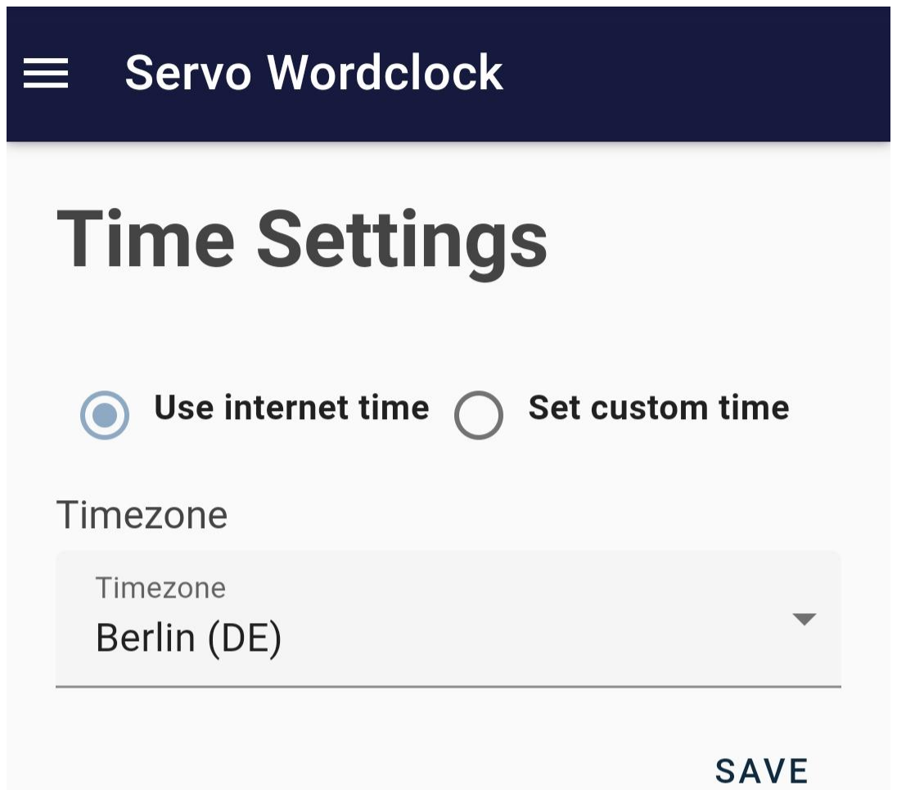
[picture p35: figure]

- If your clock is connected to the internet it will automatically receive the current time according to your configured timezone.
- To configure your local timezone enter the Time Settings menu. Select Use internet time and then choose your timezone in the field below. Clicking SAVE will update the timezone and store it in the clock’s memory
3.3.2. Manual Time Setting
- If your clock is not connected to the internet or cannot synchronize to the NTP server you can set the time manually .

2

- Go to the Time Settings menu and select Set custom time. Enter the current time and date in the fields below. The time will be updated after clicking SAVE

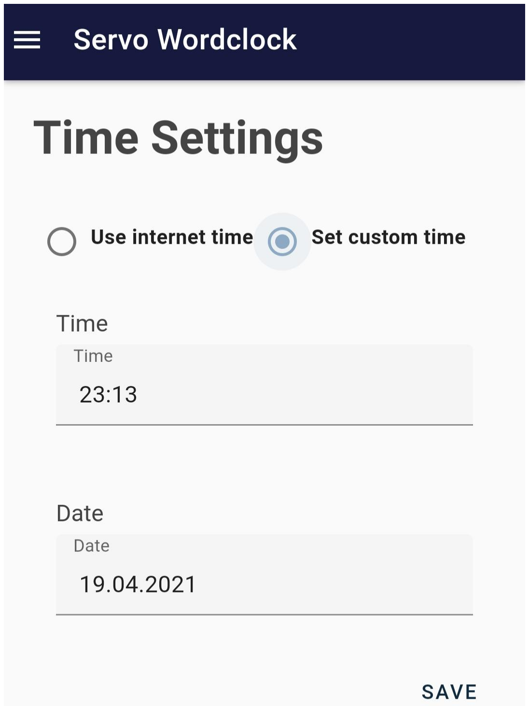
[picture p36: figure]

2 When the time is not regularly updated via NTP timekeeping may not be accurate

page 7 | v2 10-Oct-2021

### 3.4. Display Settings

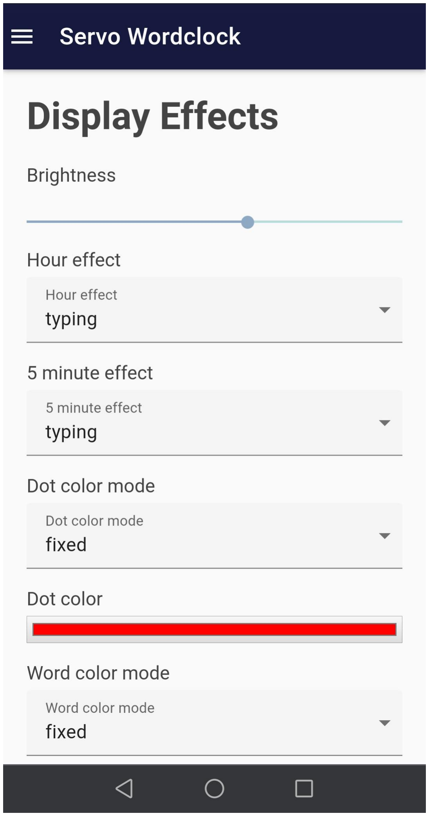
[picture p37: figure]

- The Display Effects tab can be used to change several options on how the clock displays time
- Brightness: adjusts the brightness of all LEDs
- Hour effect: selects the animation that is used to display the time every full hour. Four different effects can be used typing, fade-in, fade-out, colormix. When set to random effect one of the four effects will be randomly selected
- 5 minute effect: selects the display animation that is shown every 5 minutes. Options are similar to Hour effect
- Dot color mode: when fixed is selected the color of the minute dots can be specified in the field below. Selecting random will use a random color each time the clock updates time
- Word color mode: changes how the color of all words that are used to display the time is selected. Options are similar to Dot color mode
- Background color mode: changes how the color of all background letters that are not used to display the time is selected. Options are fixed, random and cycle. The latter will slowly cycle the color of all background letters
- Clicking SAVE will update the display and store all settings in the clock’s memory
page 8 | v2 10-Oct-2021

### 3.5. Night Mode Settings

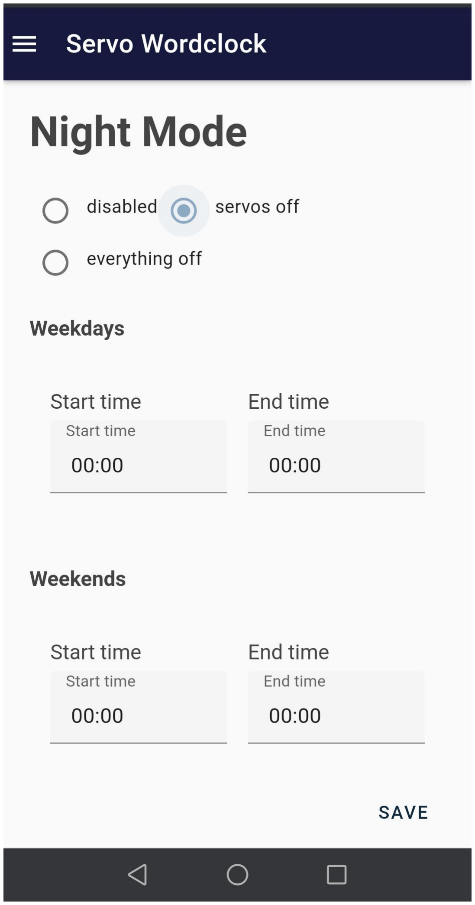
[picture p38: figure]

- The Night Mode tab can be used to either switch off the servos or the entire clock for certain periods, e.g. during the night or work hours. This will increase the lifetime of the servos and may also be used to avoid being disturbed by the noise of the servos during nighttime
- disabled: the clock will always be on
- servos off: switches off the servos for the periods defined below. The LEDs will still light up
- everything off: turns off the entire clock during the periods defined below
- Start/End time: specifies the start and end time when night mode is active. Separate periods for weekdays and weekends can be selected
- Clicking SAVE will update the settings and store them in the clock’s memory
page 9 | v2 10-Oct-2021

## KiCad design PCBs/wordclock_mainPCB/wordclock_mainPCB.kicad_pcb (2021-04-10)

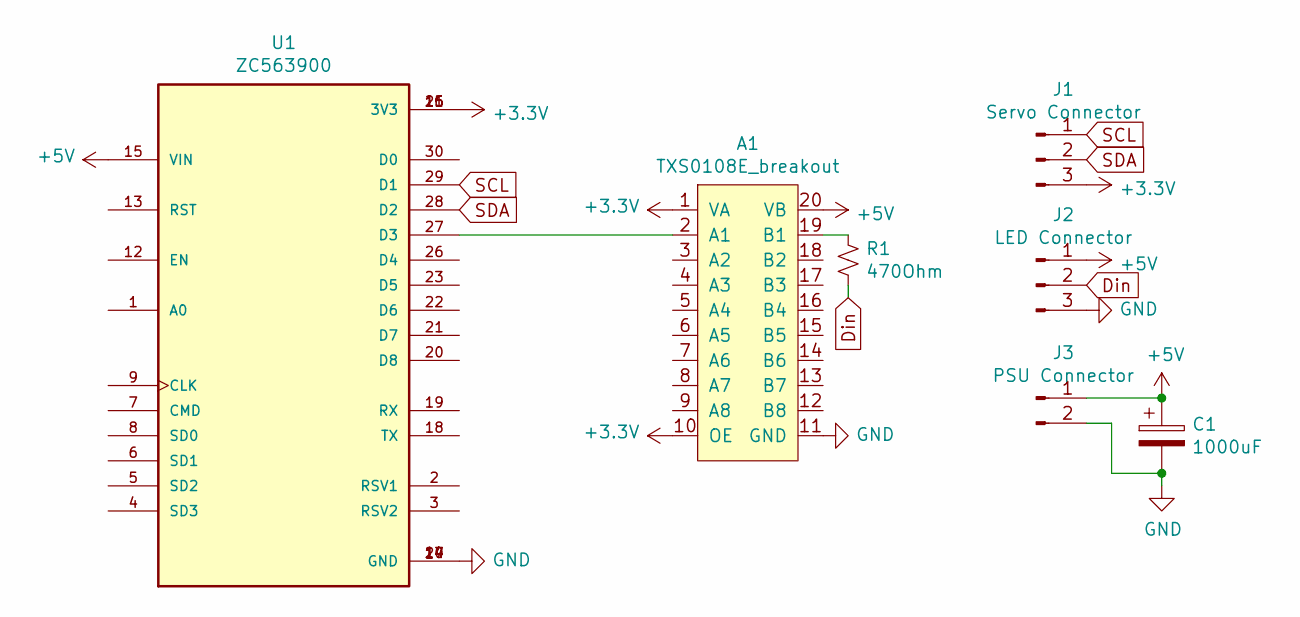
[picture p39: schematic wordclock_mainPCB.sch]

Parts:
A1: TXS0108E_breakout
C1: 1000uF; CP_Radial_D8.0mm_P3.50mm
J1: Servo Connector; PinSocket_1x03_P2.54mm_Vertical
J2: LED Connector; JST_XH_B3B-XH-A_1x03_P2.50mm_Vertical
J3: PSU Connector; JST_XH_B2B-XH-A_1x02_P2.50mm_Vertical
R1: 470Ohm; R_Axial_DIN0207_L6.3mm_D2.5mm_P10.16mm_Horizontal
U1: ZC563900; MODULE_ZC563900; PARTREV 1.0

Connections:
+3V3: A1.1 (VA), A1.10 (OE), J1.3, U1.11 (3V3), U1.16 (3V3), U1.25 (3V3)
+5V: A1.20 (VB), C1.1, J2.1, J3.1, U1.15 (VIN)
Din: J2.2, R1.1
GND: A1.11 (GND), C1.2, J2.3, J3.2, U1.10 (GND), U1.14 (GND), U1.17 (GND), U1.24 (GND)
unnamed: A1.2 (A1), U1.27 (D3)
unnamed: A1.19 (B1), R1.2
SCL: J1.1, U1.29 (D1)
SDA: J1.2, U1.28 (D2)

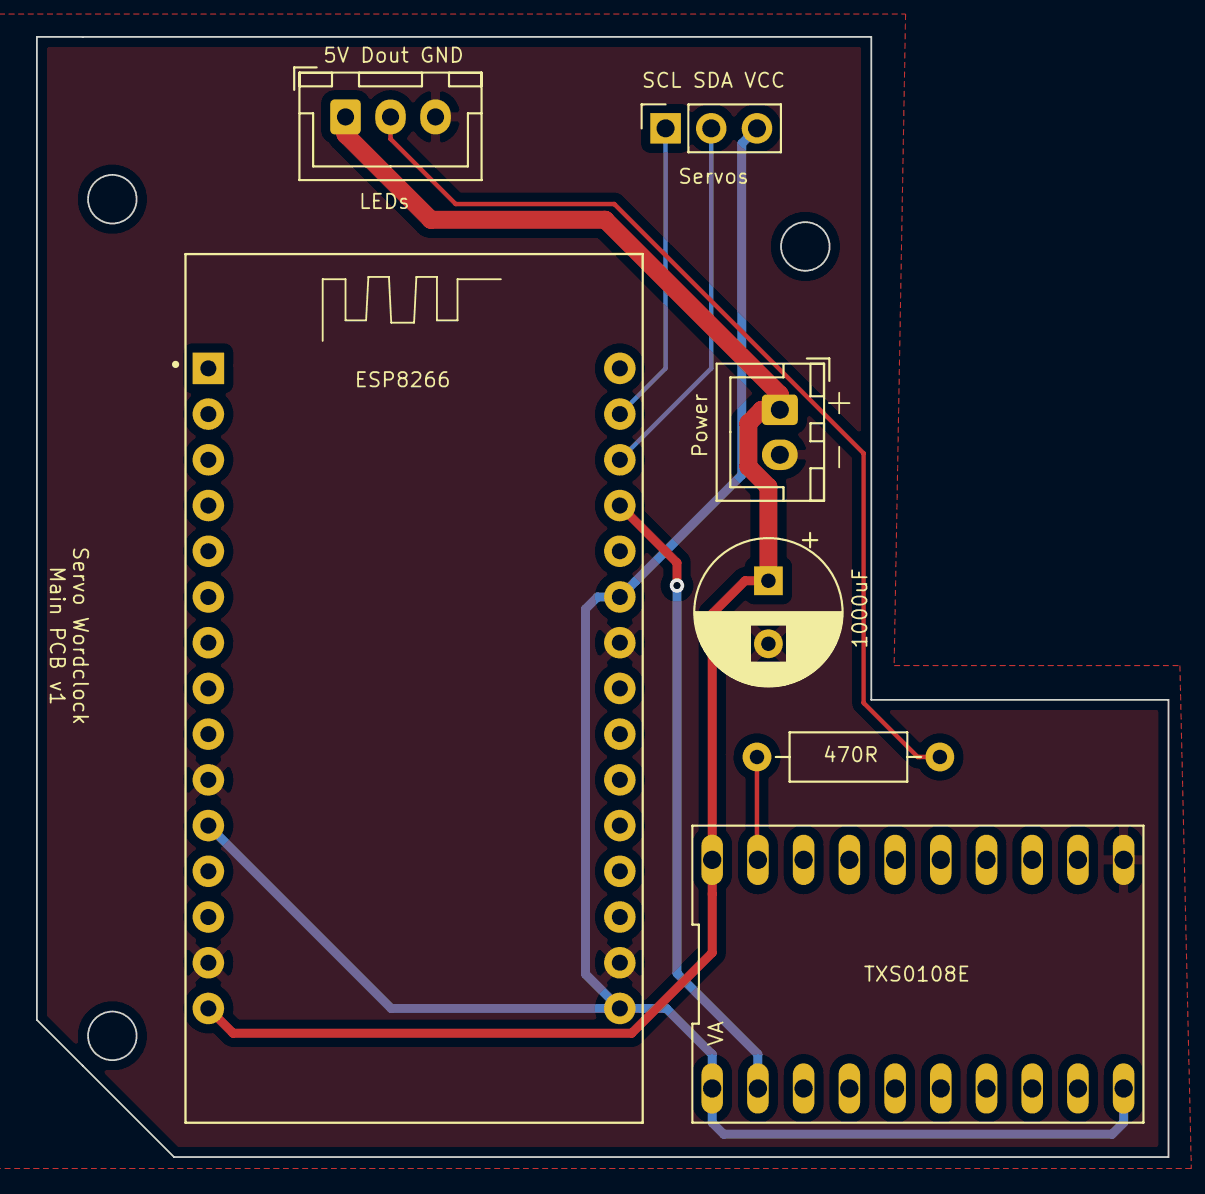
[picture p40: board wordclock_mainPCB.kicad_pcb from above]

Board: 2 copper layers, 62.9 x 62.2 mm, 7 parts (0 on the bottom side), 8 nets.

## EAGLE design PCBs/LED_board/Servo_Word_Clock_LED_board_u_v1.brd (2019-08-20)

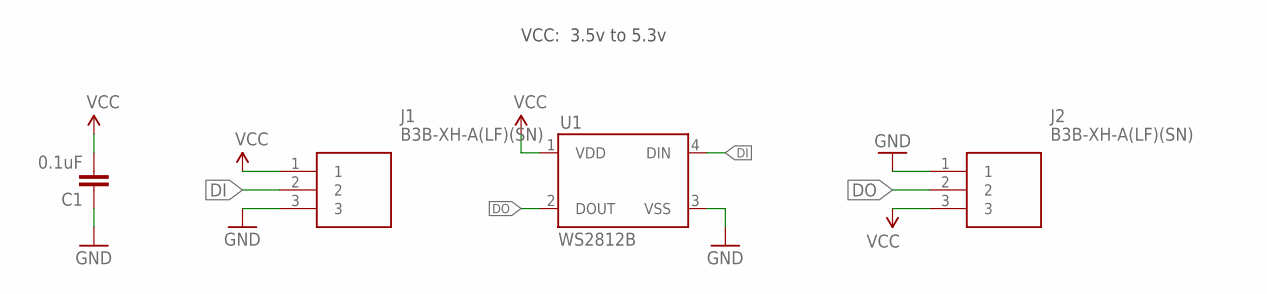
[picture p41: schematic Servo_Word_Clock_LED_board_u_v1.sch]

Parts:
C1: 0.1uF; 0603-CAP
J1, J2: B3B-XH-A(LF)(SN); SHDR3W64P0X250_1X3_990X575X700
U1: WS2812B

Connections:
DI: J1.2, U1.4 (DIN)
DO: J2.2, U1.2 (DOUT)
GND: C1.1, J1.3, J2.1, U1.3 (VSS)
VCC: C1.2, J1.1, J2.3, U1.1 (VDD)

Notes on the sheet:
VCC: 3.5v to 5.3v

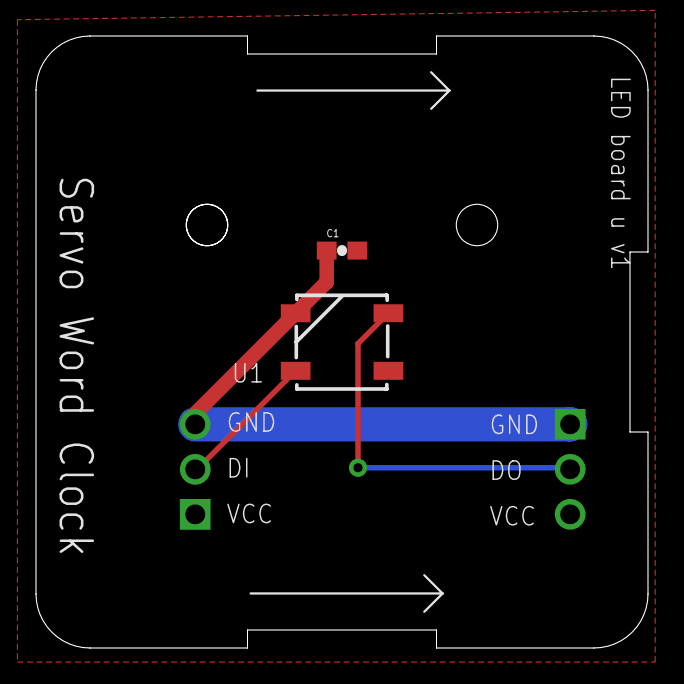
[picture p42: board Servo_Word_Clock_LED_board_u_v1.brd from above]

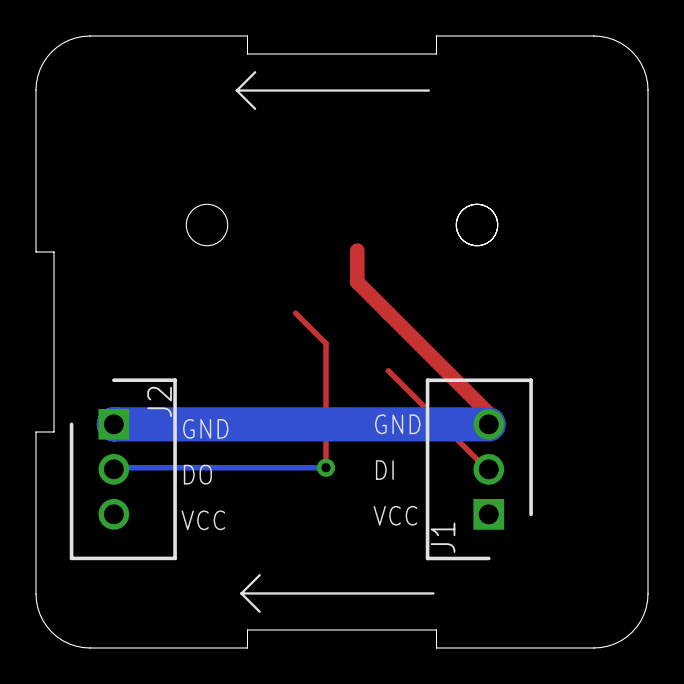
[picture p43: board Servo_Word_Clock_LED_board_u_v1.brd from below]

Board: 2 copper layers, 34.0 x 34.0 mm, 4 parts (2 on the bottom side), 4 nets.

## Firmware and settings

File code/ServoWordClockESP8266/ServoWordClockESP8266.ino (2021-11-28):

/*
    This file is part of Servo Wordclock.

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
    Copyright 2021, Moritz v. Sivers
 */

// Import required libraries
#include <ESP8266WiFi.h>
#include <ESP8266mDNS.h>
#include <DNSServer.h>
#include <ESPAsyncTCP.h>          // https://github.com/me-no-dev/ESPAsyncTCP
#include <ESPAsyncWebServer.h>    // https://github.com/me-no-dev/ESPAsyncWebServer
#include <LittleFS.h>
#include <time.h>                   // time() ctime()
#include <coredecls.h>              // settimeofday_cb()
#include <sys/time.h>                   // struct timeval
#include <sntp.h>                       // sntp_servermode_dhcp()
#include <TZ.h>                     // https://raw.githubusercontent.com/nayarsystems/posix_tz_db/master/zones.csv
#include <EEPROM.h>
#include <Ticker.h>
#include <ArduinoOTA.h>
#include <FastLED.h>
#include <Wire.h>
#include <Adafruit_PWMServoDriver.h>

// MCU functions
#include "global.h"
#include "NTP.h"
#include "LedMatrix_functions.h"
#include "TimeGen.h"

// api functions
#include "api_login.h"
#include "api_timesettings.h"
#include "api_nightmode.h"
#include "api_displayeffects.h"
#include "api_wifi.h"
#include "api_wifisettings.h"
#include "api_changepwd.h"

#include "WiFi_functions.h" // needs to come after api_wifi.h

// list all files in SPIFF -> TO BE REMOVED
void listAllFiles(){
  //Dir dir = SPIFFS.openDir ("");
  Dir dir = LittleFS.openDir ("/");
  while (dir.next ()) {
    Serial.println (dir.fileName ());
    Serial.println (dir.fileSize ());
  }
  dir = LittleFS.openDir ("/assets");
  while (dir.next ()) {
    Serial.println (dir.fileName ());
    Serial.println (dir.fileSize ());
  }
 
}
 
void setup(){

  // clear LEDs directly after start
  FastLED.addLeds<LED_TYPE,DATA_PIN,COLOR_ORDER>(leds, NUM_LEDS).setCorrection(TypicalLEDStrip);
  FastLED.clear();
  FastLED.show();

  // Serial port for debugging purposes
  Serial.begin(115200);
  delay(1000);
  
  Serial.println("Booting");

  randomSeed(analogRead(0));    // Seed RNG
 // create random login key
 loginkey = createRandString();

  // Initialize SPIFFS
  //if(!SPIFFS.begin()){
  if(!LittleFS.begin()){
    Serial.println("An Error has occurred while mounting SPIFFS");
    return;
  }

// delete all files in SPIFF -> TO BE REMOVED
/*
    bool formatted1 = SPIFFS.format();
    bool formatted = LittleFS.format();

    if(formatted){
    Serial.println("\n\nSuccess formatting");
  }else{
    Serial.println("\n\nError formatting");
  }
  */

  Serial.println("\n\n----Listing files----");
  listAllFiles();

  // define an EEPROM space of 512 Bytes to store data
  EEPROM.begin(512); 
  
  // just for testing clear EEPROM before start -> TO BE REMOVED!
  //ClearConfig();
  
  CFG_saved = ReadConfig();

  //  connect to WiFi or start as access point
  if (CFG_saved) {
    startSTA();
  }
  else {
    DefaultConfig();
    WriteConfig();
    startAP();
  }
  printConfig();

  //startSTA(); // TO BE REMOVED!!

  // start web server 
  startServer();

  // OTA configuration
  String hname = "ServoWordClock-" + String(ESP.getChipId(),HEX);
  ArduinoOTA.setHostname(hname.c_str());
  ArduinoOTA.setPassword((const char *)"ServoWordClockOTA");
  
  ArduinoOTA.onStart([]() {
    Serial.println("Start");
  });
  ArduinoOTA.onEnd([]() {
    Serial.println("\nEnd");
  });
  ArduinoOTA.onProgress([](unsigned int progress, unsigned int total) {
    Serial.printf("Progress: %u%%\r", (progress / (total / 100)));
  });
  ArduinoOTA.onError([](ota_error_t error) {
    Serial.printf("Error[%u]: ", error);
    if (error == OTA_AUTH_ERROR) Serial.println("Auth Failed");
    else if (error == OTA_BEGIN_ERROR) Serial.println("Begin Failed");
    else if (error == OTA_CONNECT_ERROR) Serial.println("Connect Failed");
    else if (error == OTA_RECEIVE_ERROR) Serial.println("Receive Failed");
    else if (error == OTA_END_ERROR) Serial.println("End Failed");
  });
  ArduinoOTA.begin();

  // initialize servo controller boards
  initServos(); 

  // only reset servos if clock is in normal mode
  currentMode = config.clockmode;    
  if(currentMode == 0) {
    initMatrix();
    sleepServos(); // disable pwm outputs to reduce humming
  }

  // initialize servo position variables
  initCurrentPos();
  
  lastmin = tm.tm_min; // initialize last update of display
 
  // start internal time update ISR
  tkSecond.attach(1, ISRsecondTick);

  // install callback - called when settimeofday is called (by SNTP or user)
  // once enabled (by DHCP), SNTP is updated every hour by default
  // ** optional boolean in callback function is true when triggerred by SNTP **
  settimeofday_cb(time_is_set);

  // configure NTP
  initNTP();

  // Give now a chance to the settimeofday callback,
  // because it is *always* deferred to the next yield()/loop()-call.
  yield();

  Serial.println("Setup done");
}
 
void loop(){
  ArduinoOTA.handle();
  dnsServer.processNextRequest();

  if  (WIFI_connected != WL_CONNECTED and time_was_set == false) {
    LED_no_wifi();
    ntpAnimation = false;
  }
  else if (WIFI_connected == WL_CONNECTED and time_was_set == false) {
    LED_no_ntp();
  }
  else if (time_was_set){
    Gen_Time();
    // if wifi connection got lost attempt reconnect
    if (WIFI_connected == WL_CONNECTED and WiFi.status() != WL_CONNECTED) {
      reconnectSTA();
      startServer();
    }
    ntpAnimation = false;
  }
}

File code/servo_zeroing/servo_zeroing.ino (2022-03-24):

// based on I2C Scanner written by Nick Gammon
// 

#include <Wire.h>
#include <Adafruit_PWMServoDriver.h>

int MAXPOS = 750;
int MINPOS = 400;

void setup() {
  Serial.begin (115200);

  // Leonardo: wait for serial port to connect
  while (!Serial) 
    {
    }

  Serial.println ();
  Serial.println ("I2C scanner. Scanning ...");
  byte address;
  
  Wire.begin();
  for (address = 1; address < 127; address++)
  {
    Wire.beginTransmission (address);
    if (Wire.endTransmission () == 0)
      {
      Serial.print ("Found address: ");
      Serial.print (" (0x");
      Serial.print (address, HEX);
      Serial.println (")");
      break;
      } // end of good response
  } // end of for loop

  Adafruit_PWMServoDriver pwm = Adafruit_PWMServoDriver(&Wire, address);

  pwm.begin();
  
  pwm.setPWMFreq(120);


  for(int servonum=0; servonum<16; servonum++) {
    pwm.setPWM(servonum, 0, MAXPOS);
    delay(400);
  }

 delay(2000);
 
  for(int servonum=0; servonum<16; servonum++) {
    pwm.setPWM(servonum, 0, MINPOS);
    delay(400);
  }

}  // end of setup

void loop() {
  
  
  }

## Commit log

2019-08-20 PCB files added
    [Servo_Word_Clock_LED_board_u_v1.brd, Servo_Word_Clock_LED_board_u_v1.sch, Servo_Word_Clock_LED_board_u_v1_BOM.xls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]
2019-11-21 bug fixes
    night mode start time can now be larger than end time
    [LedMatrix_functions.h]
2019-11-25 added advanced config
    added hidden advanced config options, random color bug fix, deleted other files, added lincense statement
    [LedMatrix_functions.h, WiFi_functions.h, global.h]
2019-11-27 new transition between clock modes
    initialize servo position according to current clockmode; servos move slowly when changing clock mode to silent or off
2019-12-01 removed servo sleep, reassigned pins
    servo sleep mode removed, LED pin newly assigned, "no NTP" animation fixed
    [LedMatrix_functions.h]
2020-05-04 Added ESP8266 compatibility
    Code made compatible with ESP8266
    Fixed Exception(3) bug
    Added asynchronous WiFi search
    [LedMatrix_functions.h, WiFi_functions.h, global.h]
2020-05-15 no NTP animation removed
    removed fade-in/out of clock symbol since it glitches on ESP8266
    corrected PCA9685 address
    [LedMatrix_functions.h]
2021-02-01 changed ESP Filesystem, bugfixing
    [ServoWordClockESP8266.ino, global.h]
2021-04-10 changed folder structure
    [Servo_Word_Clock_LED_board_u_v1.brd, Servo_Word_Clock_LED_board_u_v1.sch, Servo_Word_Clock_LED_board_u_v1_BOM.xls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]
2021-04-18 bug fixing in GUI
    [global.h]
2021-08-22 mDNS fix
    fixed mDNS
    fixed minimum brightness
    set default color and effects to random
    [ServoWordClockESP8266.ino, WiFi_functions.h, global.h]
2021-10-10 added manual and buglist, updated clearFirmware.ino
    [ClearFirmware.ino]
2021-11-04 sleepmode for servos
2021-11-28 updated for Adafruit Servo Library 2.4.0
2021-12-12 servomax position increased to 800
2022-03-24 added stl, dxf files
    added asssembly instructions, BoM, dxf, stl files
    [A V3_15.stl, B V3_15.stl, BOM.xls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]
2022-03-25 updated BoM and assembly instructions
    [BOM.xls]
2022-03-27 updated Assembly instructions
2022-05-02 added stl files
    [alignment jig.stl, glueing jig.stl]
2022-05-04 added different gear diameters
    [Spur Gear M1 Z20 - D4,85.stl, Spur Gear M1 Z20 - D4,9.stl, Spur Gear M1 Z20 - D4,95.stl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]
2025-06-24 Bump pbkdf2 from 3.1.1 to 3.1.3 in /code/servowordclock-gui-develop
    Bumps [pbkdf2](https://github.com/crypto-browserify/pbkdf2) from 3.1.1 to 3.1.3.
    - [Changelog](https://github.com/browserify/pbkdf2/blob/master/CHANGELOG.md)
    - [Commits](https://github.com/crypto-browserify/pbkdf2/compare/v3.1.1...v3.1.3)
    ---
    updated-dependencies:
    - dependency-name: pbkdf2
    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

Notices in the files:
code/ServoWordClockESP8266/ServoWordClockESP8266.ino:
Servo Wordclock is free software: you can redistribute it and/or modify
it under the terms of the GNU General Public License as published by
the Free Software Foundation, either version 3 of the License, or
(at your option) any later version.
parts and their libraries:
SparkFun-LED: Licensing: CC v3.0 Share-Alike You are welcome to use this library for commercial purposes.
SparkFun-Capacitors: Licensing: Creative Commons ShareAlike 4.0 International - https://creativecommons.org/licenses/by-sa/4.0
